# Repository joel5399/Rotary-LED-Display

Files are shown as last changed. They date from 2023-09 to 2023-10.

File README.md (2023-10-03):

# Rotary-LED-Display

## Idea
The concept behind this project involves rapidly rotating a rod and synchronizing the LEDs to create a discernible image.

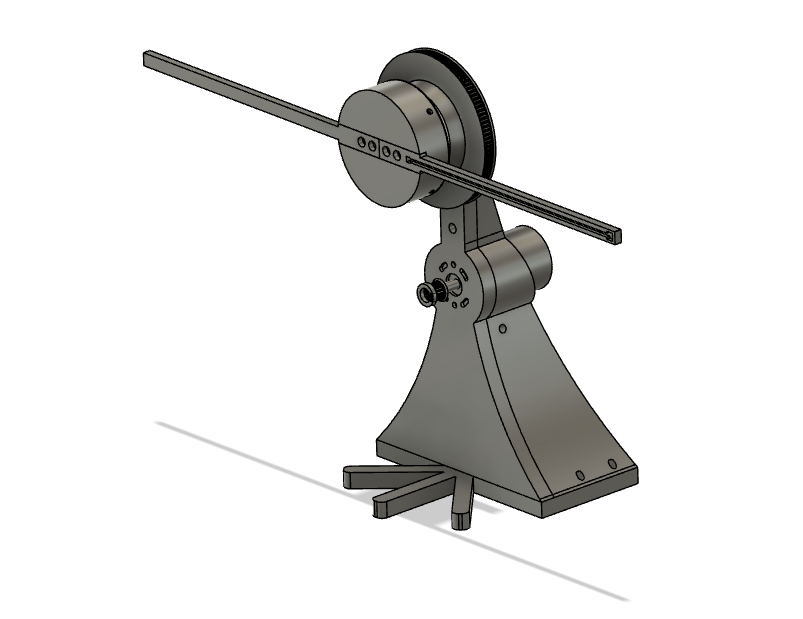
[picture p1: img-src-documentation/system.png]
3d-model


## Hardware
The entire structure is 3D printed using an FDM printer and assembled using screws. The STL files can be found in the 'printables' folder. To provide both power and data to the LEDs, I employ a [slip ring](https://www.digikey.ch/de/products/detail/adafruit-industries-llc/775/5353617?productid=5353617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). For this project, I have opted for [Dotstar LEDs](https://www.digikey.ch/de/products/detail/adafruit-industries-llc/2241/5761263?productid=5761263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) from Adafruit Industries LLC.
To measure the speed at which the LEDs are rotating, I incorporated a [hall sensor](https://www.conrad.com/p/tru-components-hall-effect-sensor-ah3661ua-24-54-v-dc-reading-range-0007-0007-t-to-92-soldering-1569221), which is mounted on the stator, along with a magnet attached to the rotating component.
For achieving consistent rotation, I employed a [DC Motor](https://www.conrad.ch/de/p/motraxx-sr555shp-3247s-75-universal-brushed-elektromotor-5887-u-min-244478.html) along with a [timing belt](https://www.conrad.ch/de/p/reely-zahnflachriemen-aeusserer-umfang-380-mm-anzahl-zaehne-152-209524.html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) to achieve the appropriate transmission. To secure the pinion to the motor shaft, I also utilized a [small pinion](https://www.conrad.ch/de/p/reely-motorritzel-modul-typ-48-dp-bohrungs-o-3-2-mm-anzahl-zaehne-12-220035.html) that can be easily mounted onto the motor shaft. To get smooth and frictionless rotation, I used two [bell-bearing](https://www.conrad.ch/de/p/ubc-bearing-61804-2z-rillenkugellager-radial-bohrungs-o-20-mm-aussen-durchmesser-32-mm-drehzahl-max-19000-u-min-197384.html).

Initially, I attempted to control the LEDs using an Arduino Uno. However, after conducting a few tests, I discovered that the operating speed of the Uno was insufficient. Consequently, I made the switch to a [Raspberry Pi 1b](https://www.sparkfun.com/products/retired/11546) for improved performance.

## Electronic
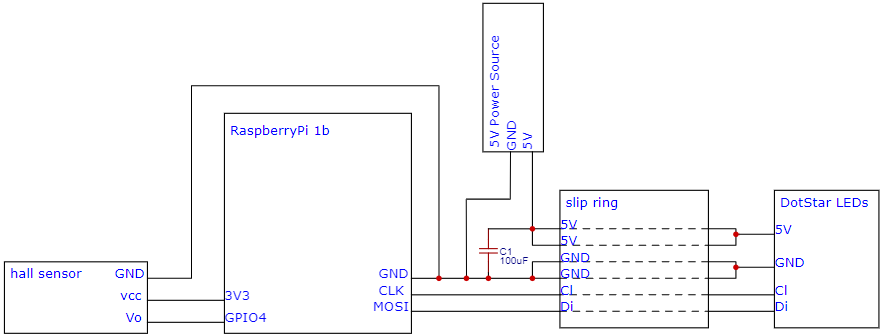
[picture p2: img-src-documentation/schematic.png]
schematic


## Software
To compile the program, please copy the '/code/display_rpi' folder to your Raspberry Pi. You can use the following command for this task:
```
scp -r /path/to/your/local/directory pi@your.pi.ip.address:/path/on/remote/pi
```
Alternatively, you can also clone this repository to your Raspberry Pi.

Certain functionalities in the program rely on OpenCV. If OpenCV is not already installed on your Raspberry Pi, please run the following command to install it:
```
sudo apt-get install libopencv-dev
```
Additionally, the program utilizes the pigpio library for GPIO control. You can locate the required file for loading this library in the 'display_rpi/cmake' folder, and it should be automatically downloaded during the compilation process.

### Compilation
Begin by creating a "build" folder within your project directory. Navigate into this newly created "build" directory. To build the project, execute the following command:
```
cmake ..
```
If CMake is not installed, you can do this with this command:
```
sudo apt-get install cmake
```
Once all the files have been built, you can compile your project using the following command:
```
make
```

### Execution
Before you can execute the program, you will need to initiate the pigpio daemon with the command:
```
sudo pigiod
```
This step only needs to be performed once after startup.

Now, within the "build" folder, you can launch the program and witness its magic in action. The program expects the absolute path to the image you want to display as an argument:

```
./display_rpi ~/display_rpi/img-src/image.jpg

```

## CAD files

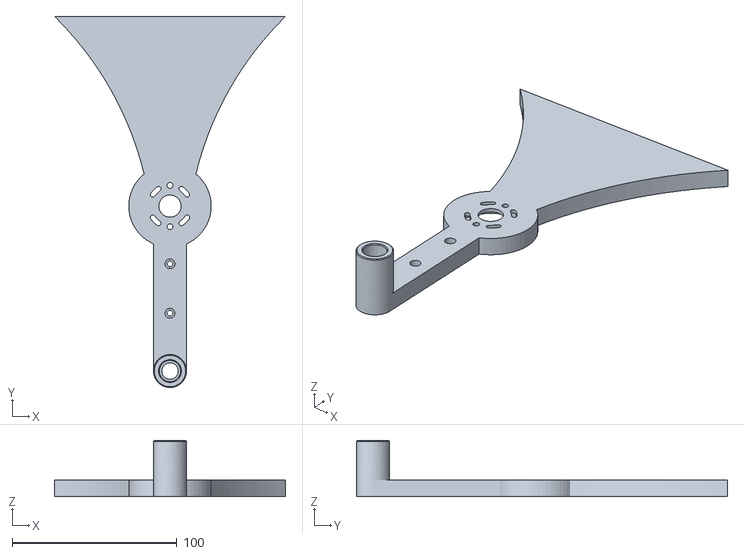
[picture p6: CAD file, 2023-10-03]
3d-files/stl-files/base-upper-part.stl
140.1 x 225.0 x 34.0

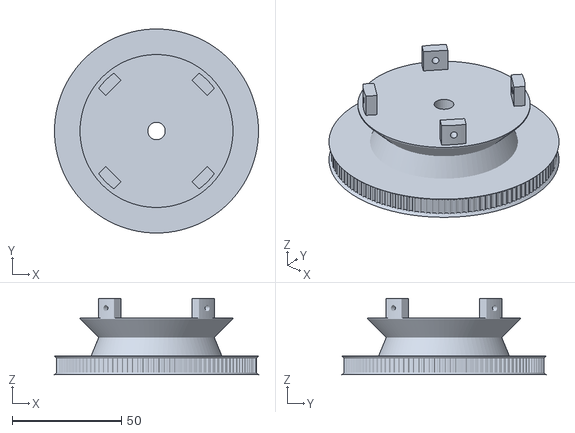
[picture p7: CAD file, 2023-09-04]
printables1/Mittelteil.stl
93.4 x 93.4 x 35.0

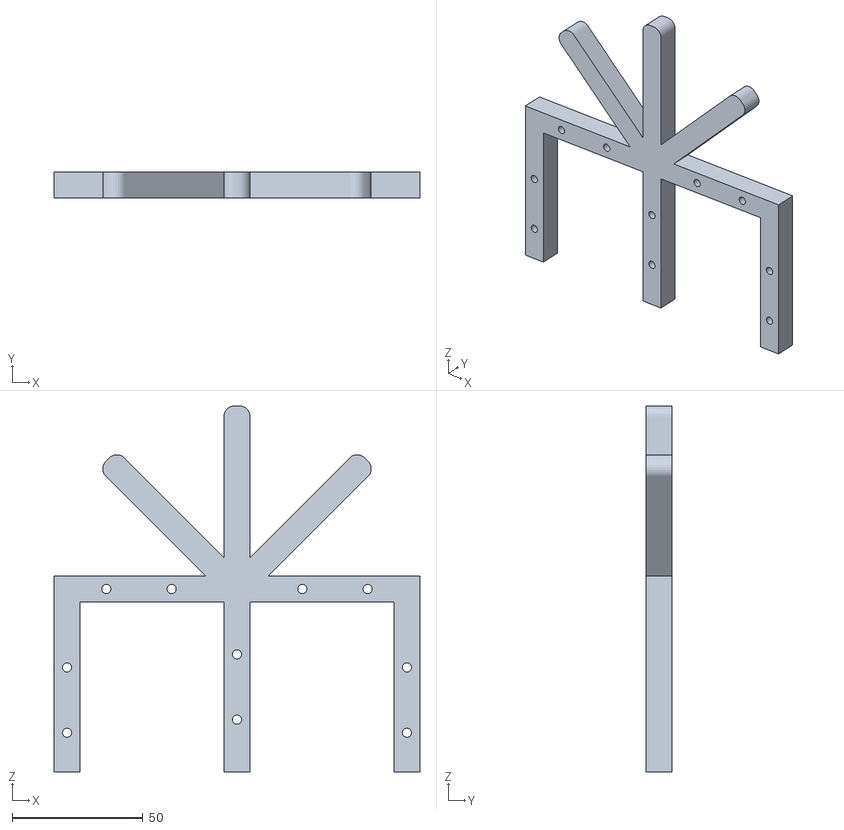
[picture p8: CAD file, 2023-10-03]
3d-files/stl-files/base.stl
140.1 x 10.0 x 140.1

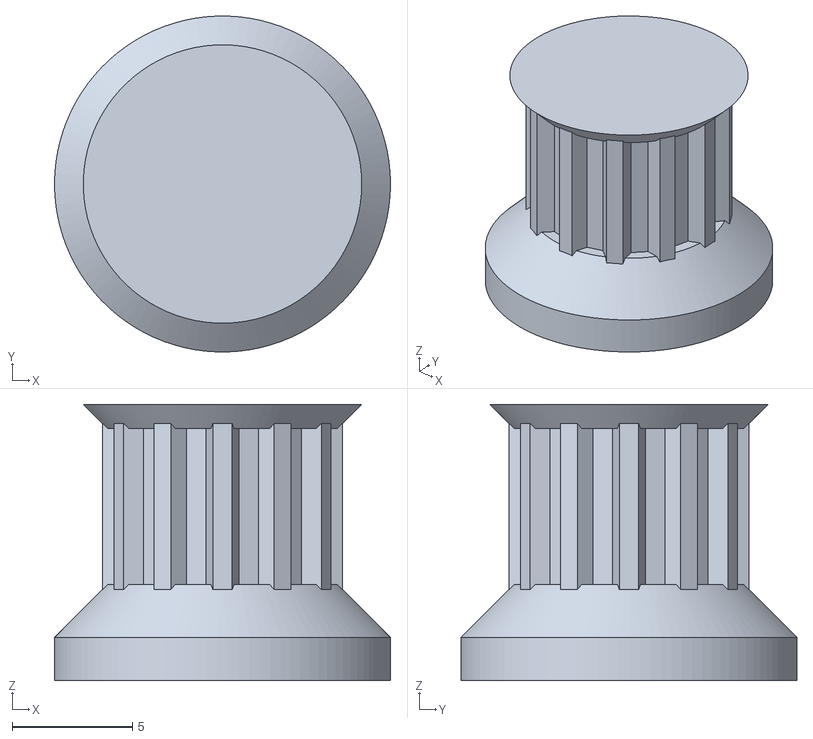
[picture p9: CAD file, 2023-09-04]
printables1/Motor_Zahnrad_2.stl
14.0 x 14.0 x 11.5

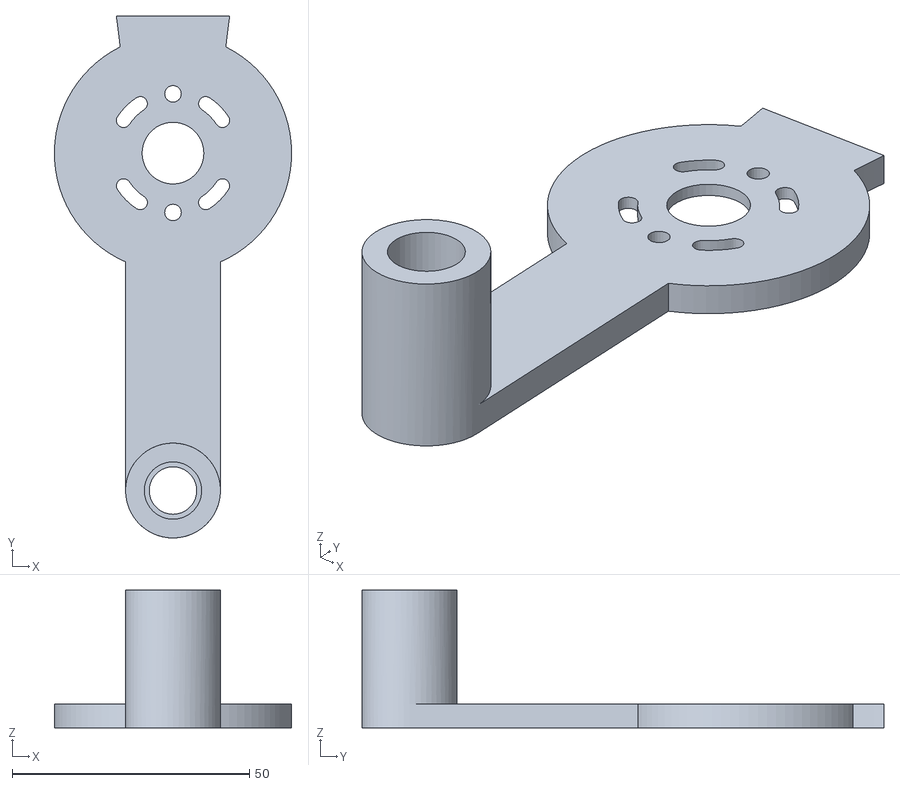
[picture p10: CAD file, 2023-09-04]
printables1/Test02_Stator.stl
50.0 x 110.0 x 29.0

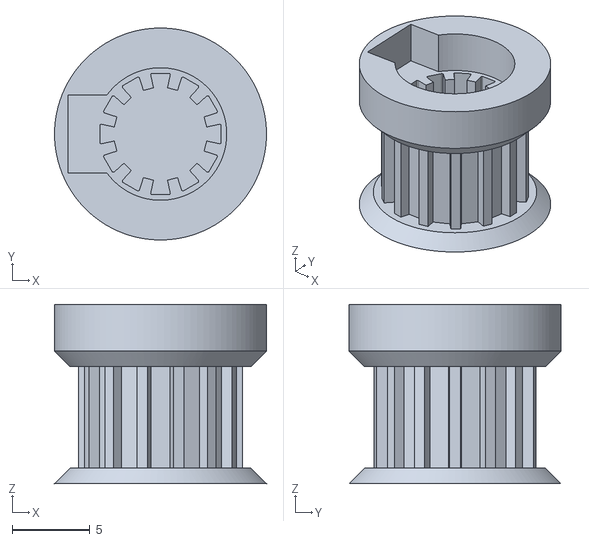
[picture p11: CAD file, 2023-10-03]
3d-files/stl-files/gear-small.stl
13.6 x 13.6 x 11.5

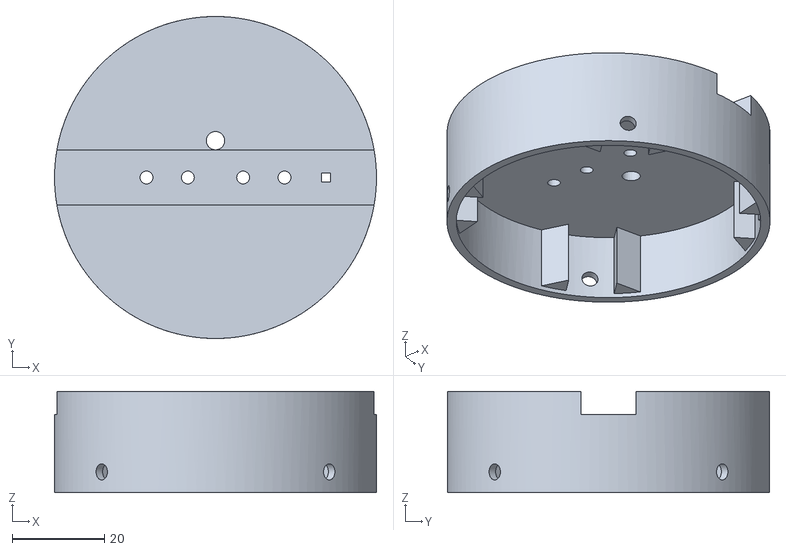
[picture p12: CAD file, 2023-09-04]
printables1/Dreh_Mitte.stl
70.0 x 70.0 x 22.0

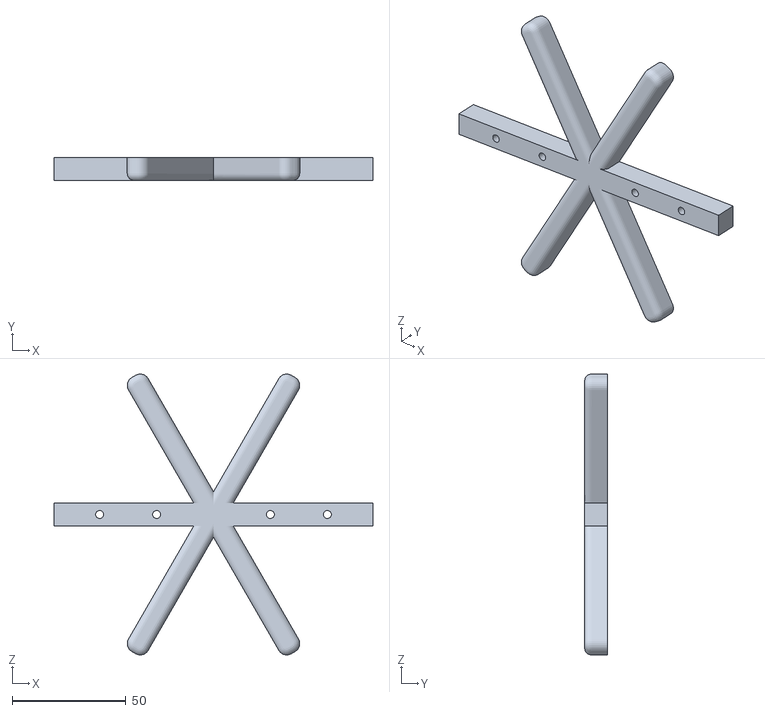
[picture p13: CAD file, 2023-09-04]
printables1/Fuss.stl
140.1 x 10.0 x 123.3

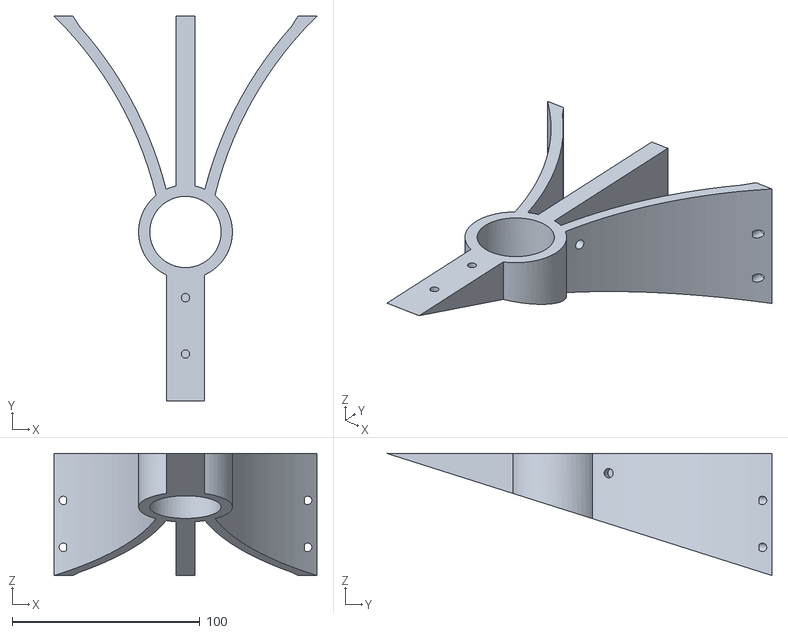
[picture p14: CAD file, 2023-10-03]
3d-files/stl-files/stabilisation-upper-part.stl
140.1 x 205.0 x 65.0

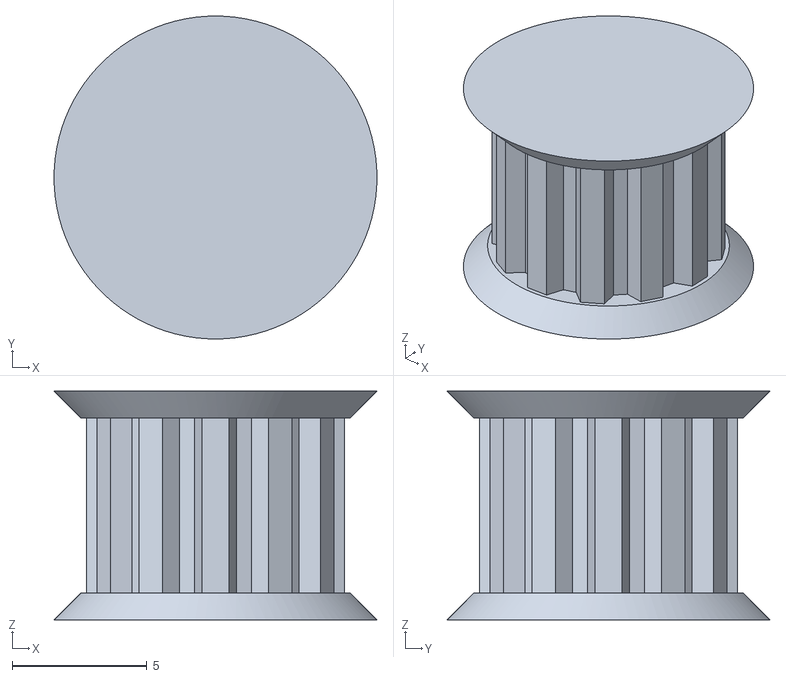
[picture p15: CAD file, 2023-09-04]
printables1/Zahnrad.stl
12.0 x 12.0 x 8.50

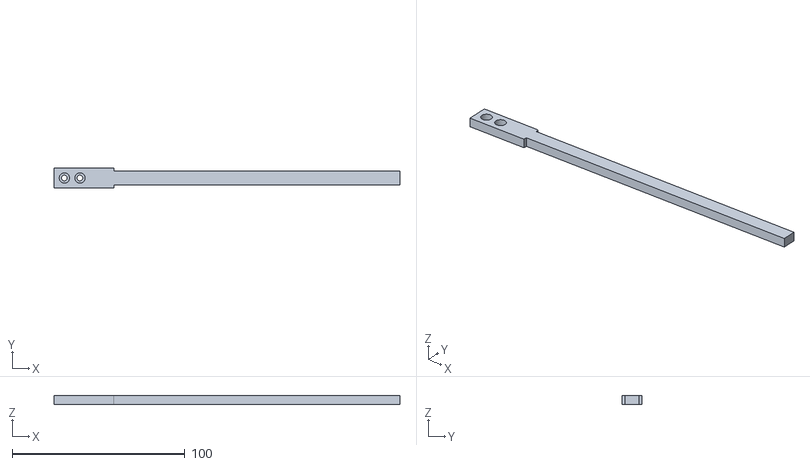
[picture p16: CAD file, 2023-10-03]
3d-files/stl-files/rod-left.stl
200.0 x 11.8 x 5.00

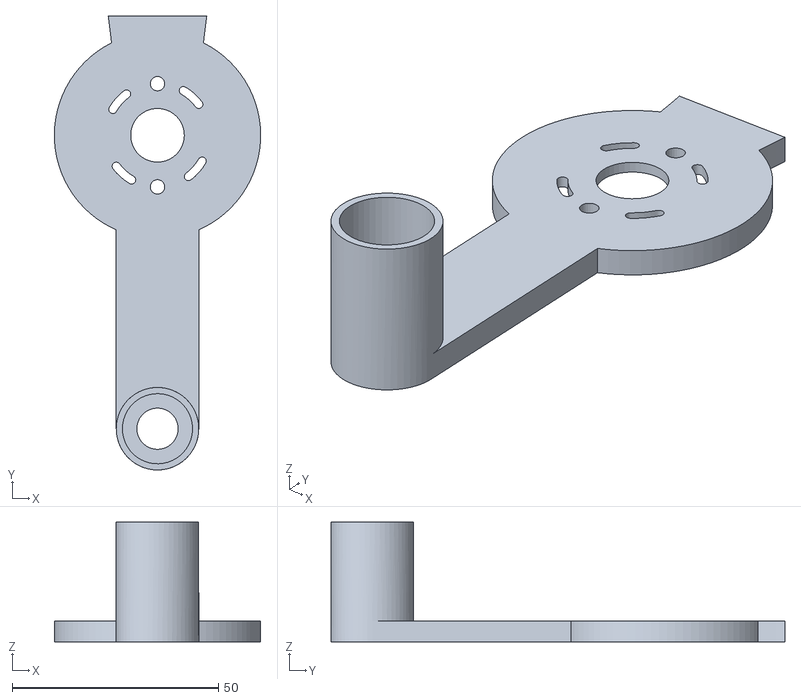
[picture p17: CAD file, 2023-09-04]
printables1/Test01_Stator.stl
50.0 x 110.0 x 29.0

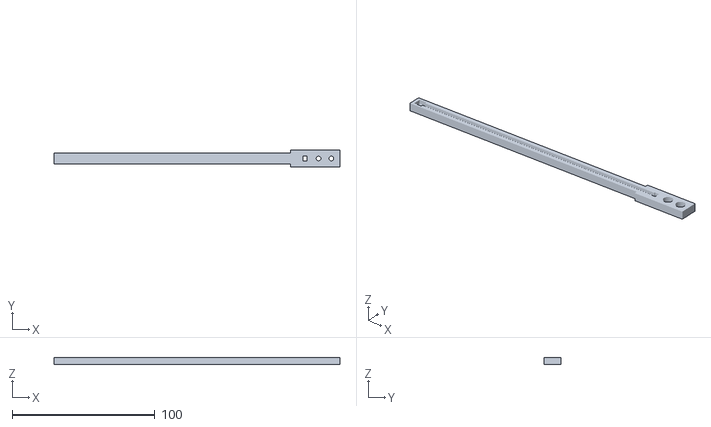
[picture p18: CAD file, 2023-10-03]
3d-files/stl-files/rod-right.stl
200.0 x 11.8 x 5.00

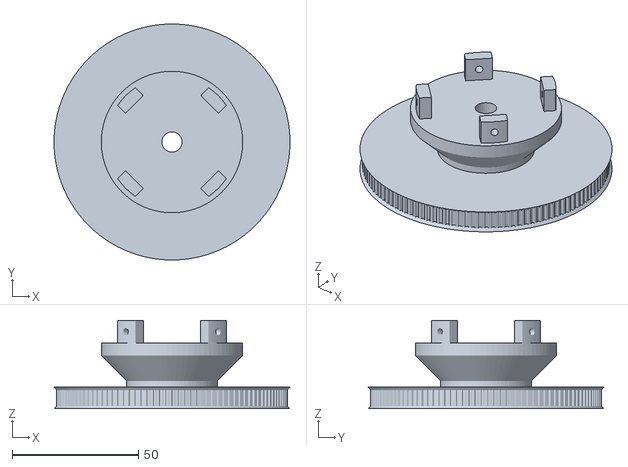
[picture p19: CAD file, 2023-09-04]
printables1/Mittel_DrehTeil.stl
93.4 x 93.4 x 35.0

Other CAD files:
3d-files/stl-files/gear-big.stl
3d-files/stl-files/middle-part-rotation.stl
printables1/Motor_Zahnrad.stl
printables1/Test03_Stator.stl
3d-files/rotary-LED-display.f3d
dataSheets/16021000/16021000.stp
dataSheets/16051200/16051200.stp
dataSheets1/16021000/16021000.stp
dataSheets1/16051200/16051200.stp
printables1/Drehstab_M_Hall.stl
printables1/Drehstab_O_Hall.stl
printables1/Motor_Zahnrad_3.stl
printables1/Stator.stl
printables1/Test_Slipring.stl
printables1/Test_Stator.stl
printables1/Test_mittelteil.stl

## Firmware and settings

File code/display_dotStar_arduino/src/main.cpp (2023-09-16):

/* Titel: Turbo Display
*  Beschreibung: Ein LED Band rotiert so schnell, dass ein Bild entsteht!
*  Autor: Joel Flepp
*  Erstellungsdatum:14.10.2022
*  Änderungen:
*  28.11.2022 Erste Tests und Pinabänderungen
*  01.09.2023 Weiterentwcklung
*/

/*******************************************
 * Positionierung x und y
 * 
 * (conector)left    right
 *       0 1 2 3 4   5 6 7 8 9
 *    
 *       o o o o o x o o o o o
 * 
 *  /\
 *  |
 *  |_____>
 *  (0;0)
 * *****************************************/



//Includes
#include <Arduino.h>
#include <Adafruit_DotStar.h>
#include <Wire.h>
#include <SPI.h>
#include <avr/io.h>
#include <avr/interrupt.h>
#include "LED.h"
#include "Image.h"

//Pin Defines
const int dataPin = 4;
const int clockPin = 5;
const int hallSensor = 2;

//Programm const
const double angleOffset = 1.7;
const double LEDOffset = 2.5;
const double LEDDistance = 6.944444;                       // [mm]
const int LEDCount = 58;                                   // 
const uint8_t brightness = 20;                              // Set BRIGHTNESS to about 1/5 (max = 255)
const double X_Y_TO_Left_Bottom = LEDDistance * (LEDCount / 2);


//Variables
unsigned long previousTime = 0;
unsigned long cycleTime_myS = 0;
LEDClass LED[LEDCount];

//Skalierungsfaktor 
const int wingspan = LEDCount * LEDDistance; // [mm]
const double ImgScale = wingspan / sizeof(Smiley[0]); // [mm / arrayLength]


//Functions
void getCycleTime();
double getCurrentAngle();
void setLEDPosition(const int &LEDPos, const double &CurrentAngle);
void setLEDCollors(const int &LEDPos);
void UpdateLEDs();


//Classes
Adafruit_DotStar strip(LEDCount, DOTSTAR_BGR);

void setup() {
    // Start Serial
    Serial.begin(115200);

    // Interrupt for HallSensor
    pinMode(hallSensor,INPUT_PULLUP);
    interrupts();
    attachInterrupt(digitalPinToInterrupt(hallSensor), getCycleTime, RISING);
    
    // Create LEDs
    for(size_t i = 0; i < LEDCount; i++) {
        LED[i].setDistance(i * LEDDistance + LEDOffset);
    }
    
    // INITIALIZE Dorstar strip object
    strip.begin();                   
    strip.setBrightness(brightness); 
    strip.clear();              
}

void loop() {
    double currentAngle = getCurrentAngle();
    //Serial.println(currentAngle);
    for(size_t i = 0; i < LEDCount; i++) {
        setLEDPosition(i,  currentAngle);
        setLEDCollors(i);
    }
    UpdateLEDs();
}

//Interrupt routine for getting the RPM from the device
void getCycleTime() {
    cycleTime_myS = micros() - previousTime;
    previousTime = micros();
}

//Calculate Angle (rad) from revolutions
double getCurrentAngle() {
    return ((double)(micros() - previousTime) / (double)(cycleTime_myS)) * 2 * 3.14 + angleOffset;
}


void setLEDPosition(const int &LEDPos, const double &CurrentAngle) {
    LED[LEDPos].setXYCartesianFromAngle(CurrentAngle, wingspan);
}


void setLEDCollors(const int &LEDPos) {
    const uint8_t xPosImg = LED[LEDPos].getXPos() / ImgScale;
    const uint8_t yPosImg = LED[LEDPos].getYPos() / ImgScale;

    LED[LEDPos].setRed(Smiley[xPosImg][yPosImg]);
    LED[LEDPos].setBlue(Smiley[xPosImg][yPosImg]);
    LED[LEDPos].setGreen(Smiley[xPosImg][yPosImg]);
}

void UpdateLEDs() {
    for(size_t i = 0; i < LEDCount; i++){
        strip.setPixelColor(i,LED[i].getRed(), LED[i].getGreen(),LED[i].getBlue());
    }
    strip.show();
}

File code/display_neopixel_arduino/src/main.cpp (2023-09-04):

/* Titel: Turbo Display
*  Beschreibung: Ein LED Band rotiert so schnell, dass ein Bild entsteht!
*  Autor: Joel Flepp
*  Erstellungsdatum:14.10.2022
*  Änderungen:
*  28.11.2022 Erste Tests und Pinabänderungen
*/


//Includes
#include <Arduino.h>
#include <Adafruit_NeoPixel.h>
#include "LED.h"
#include "Image.h"
#include <math.h>

//Pin Defines
#define Strip_Pin 9
#define Hall_Sens 2
#define Motor 6


//Programm Defines
#define Ard_Freq 16000000
#define LED_Distance 6.944444 //[mm]
#define LED_Count 28
#define BRIGHTNESS 50 // Set BRIGHTNESS to about 1/5 (max = 255)
#define X_Y_TO_Left_Bottom LED_Distance*LED_Count


//Variables
float RPS = 0;
double CycleTime_MyS = 0;
LED LEDsHall[LED_Count];
LED LEDs_o_Hall[LED_Count];


//Functions
void Get_RPS();
float get_Angle();
void Set_Collors();
void Set_LEDs();


//Classes
Adafruit_NeoPixel strip(LED_Count + LED_Count, Strip_Pin, NEO_GRB + NEO_KHZ800);

//Skalierungsfaktor 
uint8_t scale = 400 / sizeof(Smiley[0]);


void setup() {
  //Start Serial
  Serial.begin(115200);
  pinMode(Hall_Sens,INPUT_PULLUP);

  //Interrupt for Hallsensor
  pinMode(Hall_Sens,INPUT_PULLUP);
  interrupts();
  attachInterrupt(digitalPinToInterrupt(Hall_Sens), Get_RPS, FALLING);
  pinMode(8,INPUT_PULLUP);
  
  //Activate Timer
  TCCR1A = 0;
  TCCR1B = 0;
  TCCR1B |= (1<<CS12); //Prescaler 256
  

  //Create LEDs Right
  for(size_t i = 0; i<LED_Count; i++){
    LEDsHall[i].set_Distance(i*LED_Distance);
  }

  //Create LEDs Left
  for(size_t i = 0; i<LED_Count; i++){
    LEDs_o_Hall[i].set_Distance(i*LED_Distance);
  }  
  
  strip.begin();           // INITIALIZE NeoPixel strip object (REQUIRED)
  strip.show();            // Turn OFF all pixels ASAP
  strip.setBrightness(50); // Set BRIGHTNESS to about 1/5 (max = 255)


}

void loop() {
  //Set x and y positions of the LEDS
  if(digitalRead(8)==0){
  for(size_t i=100; i<255;i++){
    analogWrite(Motor,i);
    delay(20);
    if(digitalRead(8)==1){
      break;
    }
  }
  while(digitalRead(8)==0){

    for(size_t i = 0; i < LED_Count; i++){
      LEDsHall[i].set_x(int(sin(get_Angle())*LEDsHall[i].get_Distance())+X_Y_TO_Left_Bottom);
      LEDsHall[i].set_y(int(cos(get_Angle())*LEDsHall[i].get_Distance())+X_Y_TO_Left_Bottom);
    }

    for(size_t i = 0; i < LED_Count; i++){
      LEDs_o_Hall[i].set_x(int(-sin(get_Angle())*LEDs_o_Hall[i].get_Distance())+X_Y_TO_Left_Bottom);
      LEDs_o_Hall[i].set_y(int(-cos(get_Angle())*LEDs_o_Hall[i].get_Distance())+X_Y_TO_Left_Bottom);
    }

    //Set the Collors
    Set_Collors();
    Set_LEDs();
    //Serial.println(LEDs_o_Hall[14].get_x());

  }
  }
  else{
    analogWrite(Motor,0);
  }


}

//Interrup routine for getting the RPM from the device
void Get_RPS(){
  //With Prescaler 256, 1 Klick is 16 myS
  CycleTime_MyS = TCNT1 * 0.000016;
  RPS = 1.0 / (double)CycleTime_MyS;
  TCNT1 = 0;
}

//Calculate Angle (rad) from revolutions
float get_Angle(){
  
  double Timer_In_myS = TCNT1 * 0.000016;
  float Angle = (Timer_In_myS*2*PI) / CycleTime_MyS;
  return Angle;
}

void Set_Collors(){
  for(size_t i = 0; i < LED_Count; i++){
    LEDsHall[i].set_Red(Smiley[(uint8_t)LEDsHall[i].get_x()/scale][(uint8_t)LEDsHall[i].get_y()/scale]);
    LEDsHall[i].set_Blue(Smiley[(uint8_t)LEDsHall[i].get_x()/scale][(uint8_t)LEDsHall[i].get_y()/scale]);
    LEDsHall[i].set_Green(Smiley[(uint8_t)LEDsHall[i].get_x()/scale][(uint8_t)LEDsHall[i].get_y()/scale]);
    LEDs_o_Hall[i].set_Red(Smiley[(uint8_t)LEDs_o_Hall[i].get_x()/scale][(uint8_t)LEDs_o_Hall[i].get_y()/scale]);
    LEDs_o_Hall[i].set_Blue(Smiley[(uint8_t)LEDs_o_Hall[i].get_x()/scale][(uint8_t)LEDs_o_Hall[i].get_y()/scale]);
    LEDs_o_Hall[i].set_Green(Smiley[(uint8_t)LEDs_o_Hall[i].get_x()/scale][(uint8_t)LEDs_o_Hall[i].get_y()/scale]);

  }

}

void Set_LEDs(){
  uint8_t j = 0;

  for(size_t i = LED_Count; i > 0; i--){
    strip.setPixelColor(j,strip.Color(LEDs_o_Hall[i].get_Red(), LEDs_o_Hall[i].get_Green(),LEDs_o_Hall[i].get_Blue()));
    strip.show();                          //  Update strip to match
    delayMicroseconds(300);
    j++;
  }

  for(size_t i = 0; i < LED_Count; i++){
    strip.setPixelColor(j,strip.Color(LEDsHall[i].get_Red(), LEDsHall[i].get_Green(),LEDsHall[i].get_Blue()));
    strip.show();                          //  Update strip to match
    delayMicroseconds(300);
    j++;
  }

}

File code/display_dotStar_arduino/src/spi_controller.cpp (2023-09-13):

#include <pigpiod_if2.h>
#include "smt_movement_controller/gpio_controller.hpp"
#include "smt_movement_controller/movement_controller.hpp"

enum class Pin {
    PWM_LEFT = 4,      //!< pwm motor Left (Pyhsical 7)
    PWM_RIGHT = 5,     //!< pwm motor right (Physical 29)
    DIR_LEFT_1 = 17,   //!< direction pin left 1 (Physical 11)
    DIR_LEFT_2 = 27,   //!< direction pin left 2 (Physical 13)
    DIR_RIGHT_1 = 6,   //!< direction pin right 1 (Physical 31)
    DIR_RIGHT_2 = 13,  //!< direction pin right 2 (Physical 33)
};

const int PWM_FREQ = 20000;      //!< Hertz
const int PWM_RANGE = 100;       //!< Range for pwm 0% to 100%
const double MAX_SPEED = 0.715;  //!< m/s measured


        SpiController::SpiController() {
            this->pi = pigpio_start(NULL, NULL);
            if (this->pi < 0) {
                throw std::runtime_error("error while trying to initialize pigpio!");
                return;
            }

            // PWMs
            set_mode(this->pi, static_cast<uint>(Pin::PWM_LEFT), PI_OUTPUT);
            set_mode(this->pi, static_cast<uint>(Pin::PWM_RIGHT), PI_OUTPUT);

            set_PWM_frequency(this->pi, static_cast<uint>(Pin::PWM_LEFT), PWM_FREQ);
            set_PWM_frequency(this->pi, static_cast<uint>(Pin::PWM_RIGHT), PWM_FREQ);

            set_PWM_range(this->pi, static_cast<uint>(Pin::PWM_LEFT), PWM_RANGE);
            set_PWM_range(this->pi, static_cast<uint>(Pin::PWM_RIGHT), PWM_RANGE);

            // GPIOs
            set_mode(this->pi, static_cast<uint>(Pin::DIR_LEFT_1), PI_OUTPUT);
            set_mode(this->pi, static_cast<uint>(Pin::DIR_LEFT_2), PI_OUTPUT);
            set_mode(this->pi, static_cast<uint>(Pin::DIR_RIGHT_1), PI_OUTPUT);
            set_mode(this->pi, static_cast<uint>(Pin::DIR_RIGHT_2), PI_OUTPUT);

            gpio_write(this->pi, static_cast<uint>(Pin::DIR_LEFT_1), 0);
            gpio_write(this->pi, static_cast<uint>(Pin::DIR_LEFT_2), 0);
            gpio_write(this->pi, static_cast<uint>(Pin::DIR_RIGHT_1), 0);
            gpio_write(this->pi, static_cast<uint>(Pin::DIR_RIGHT_2), 0);
        }

        SpiController::~SpiController() {
            pigpio_stop(this->pi);
        }

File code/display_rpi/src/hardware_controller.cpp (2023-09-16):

#include "hardware_controller.hpp"


const unsigned SPI_CHANNEL = 0;
const unsigned BAUD_RATE = 8000000; //!< Baud rate for spi communication

// Definition der statischen Member-Variable
RotationController* HardwareController::rotationController = nullptr;

HardwareController::HardwareController() {
    this->pi = pigpio_start(NULL, NULL);
    if (this->pi < 0) {
        std::cout << this->pi << "\n";
        throw std::runtime_error("error while trying to initialize pigpio!");
        return;
    }

    this->spi = spi_open(this->pi, SPI_CHANNEL, BAUD_RATE, 0);
    if (this->spi < 0) {
        throw std::runtime_error("error while trying to initialize spi!");
        return;
    }
    std::cout << "pi ID: " << this->pi << "\n";
    std::cout << "spi ID: " << this->spi << "\n";

    rotationController = nullptr;
}

HardwareController::~HardwareController() {
    spi_close(this->pi, this->spi);
    pigpio_stop(this->pi);
}

int HardwareController::updateSpi(char* buf, unsigned count) const {
    int sendedData = spi_write(this->pi, this->spi, buf, count);
    return unsigned(sendedData) != count ? 1 : 0;
}

void HardwareController::setInterrupt(const unsigned& pinInterrupt, RotationController* RotationController_) {
    rotationController = RotationController_;
    int callbackId = callback(this->pi, pinInterrupt, RISING_EDGE, this->callbackFunction);
    std::cout << "callback ID: " << callbackId << "\n";
}

unsigned HardwareController::getCurrentTick() const {
    return get_current_tick(this->pi);
}

void HardwareController::callbackFunction(int pi, unsigned user_gpio, unsigned level, unsigned tick) {
    rotationController->setCurrentAngleToZero(tick);
}

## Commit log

2023-09-13 initial commit for rpi programm
    [Fuss.stl, Stator.stl, Stator_V2.stl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]
2023-10-03 complete README
    [Dreh_Mitte.stl, Drehstab_M_Hall.stl, Drehstab_O_Hall.stl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]
